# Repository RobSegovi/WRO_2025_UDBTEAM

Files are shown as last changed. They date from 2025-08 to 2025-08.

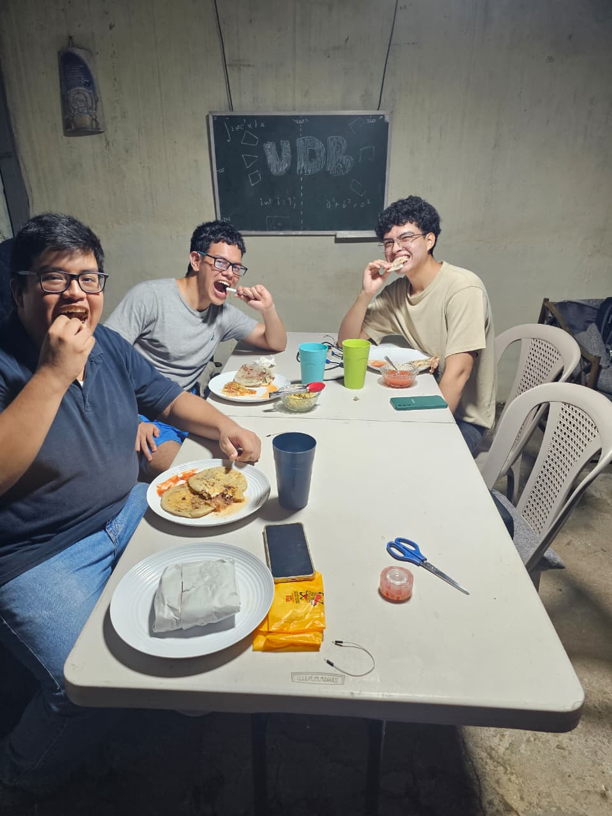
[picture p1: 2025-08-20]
T-photos/Funny Team.jpeg

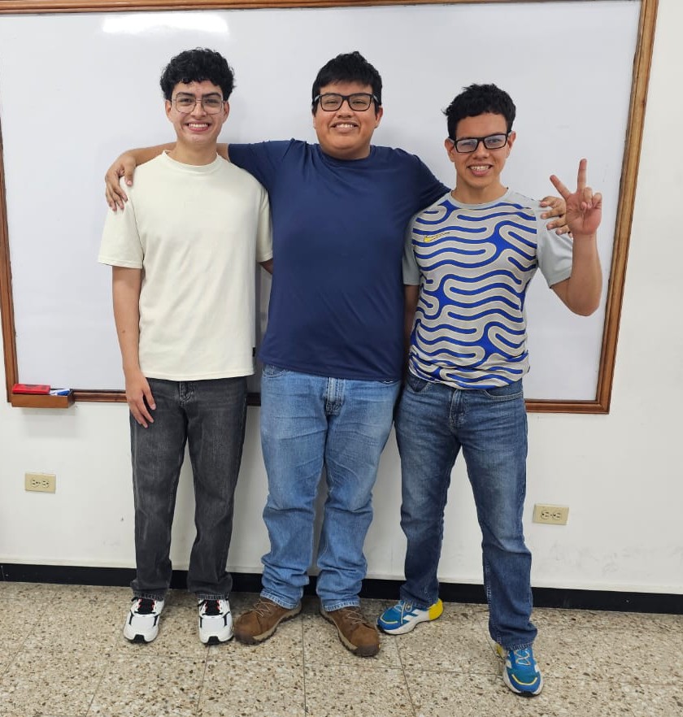
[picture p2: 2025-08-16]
T-photos/Team.jpeg

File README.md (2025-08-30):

# WRO_2025_UDBTEAM
Proyecto del vehículo autónomo para WRO 2025 - Futuros Ingenieros

<div align="center">

</div>

## Content

* `t-photos` contains 2 photos of the team 
* `video` contains the video.md file with the link to a video where driving demonstration exists
* `src` contains code of control software for all components which were programmed to participate in the competition
* `other` contains our training model for cubes based on yolo8

## Introduction
### Steering 
To control the vehicle direction, we adapted the tires form an RC car and implemented a steering mechanism that transforms the rotational motion of the servo motor (model G995) into rotational motion along a different axis as shown in image.  The servo motor provides enough torque to steer the vehicle while allowing precise control of the steering angle.



### Traction
The traction mechanism was disassembled from the RC car and integrated into the chassis of our vehicle.  The mechanism consists of three large gears that increase the torque of the DC motor, along with a smaller gear that connects the motor shaft to the three larger gears. The DC motor is controlled by an H bridge (L298 Module), which allows rotation in two directions to move the car forward and backward. The module can supply up to 35V and 2A, which is sufficient power for the motor. 



### Power sources 
A power bank  that supplies up to 5V at 3A powers the Raspberry Pi5, which requires a 5V at 5A but can also run on 5V at 3A.  The Raspberry Pi5 supplies power to the Arduino Mega via USB.
Two JYD 18650 batteries connected in series provide up to 8.2V, which is regulated to 6.5V by an LM2596 voltage regulator. This maintains a stable supply for the servo motor and H bridge, even as the batteries discharge.
Two separate power sources are used because a single power source capable of supplying both the Raspberry Pi5 and motors was not available.

<div align="center">

</div>

### Turning the car on and off
A switch connecting GND and the negative terminal of the battery is used to turn the motor and servo motor on and off. The power button on the Raspberry Pi5 is used to turn the Raspberry Pi5 and the Arduino Mega on and off.

### Articial vision
Our car can see its surroundings through a webcam connected via USB to a Raspberry Pi5, which processes the video input using python scripts with Open CV and a YOLO model trained on our dataset of images of red and green cubes.

### Information gathering Open challenge
Raspberry Pi 5 processes the information received from the webcam with three Python scripts. The main one is called xd.py and receives information from detectarcolor.py, which sends data to xd.py when it detects that enough pixels inside the area of interest fall within the blue or orange HSV threshold. xd.py also receives information from detectarpared.py when enough dark pixels are detected inside six different areas of interest: four detect the walls on the sides of the vehicle, one is positioned near the upper edge of the image to detect an incoming wall from the front, and another is located at the bottom center of the screen to detect when the vehicle is too close to a wall.

### Decision making Open challenge
The vehicle moves forward until it detects the blue or orange strips on the floor. A blue detection means the robot must steer to the right and ignore the orange strips. If an orange strip is detected, the robot does the opposite. After this, the vehicle will try to follow the inner walls, having three possible states: too close to the inner wall, close enough, or too far from the inner wall. The vehicle steers as needed to keep itself close enough to the inner wall until it detects a strip of the correct color and repeats the process.

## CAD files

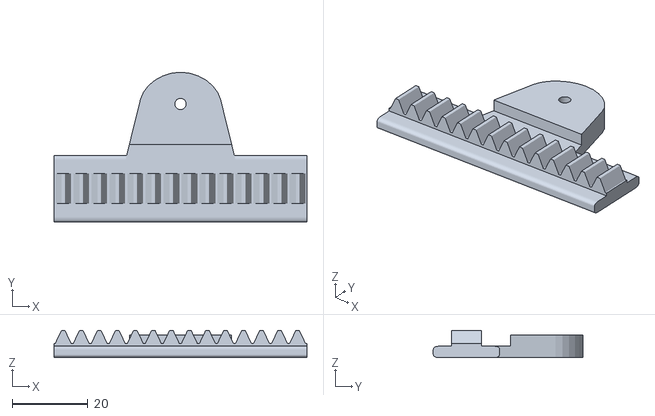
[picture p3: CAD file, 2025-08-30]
Models/Mecanismos UDB WRO/WRO-Cremallera.stl
67.0 x 39.6 x 7.18

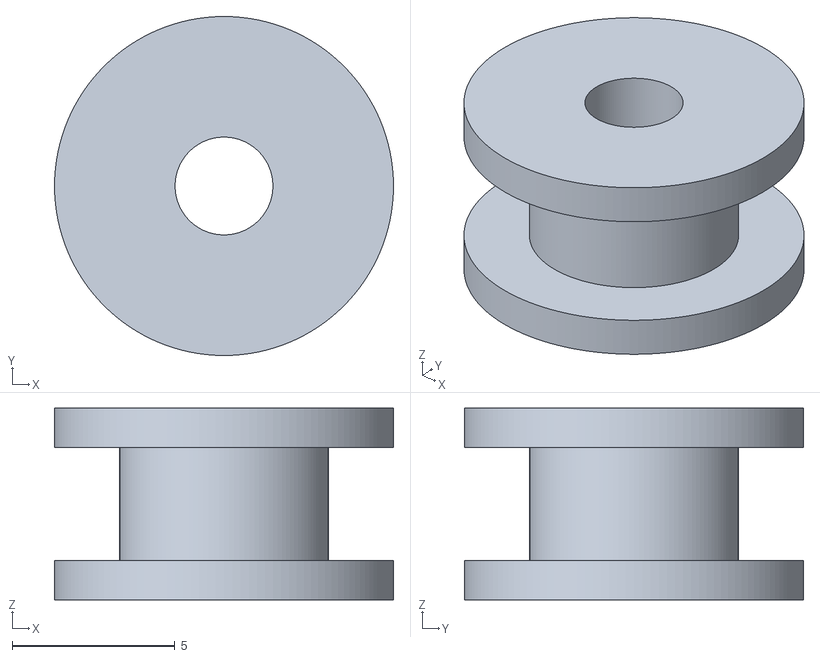
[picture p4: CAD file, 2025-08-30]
Models/Mecanismos UDB WRO/WRO-DeslizadorAcople.stl
10.4 x 10.4 x 5.88

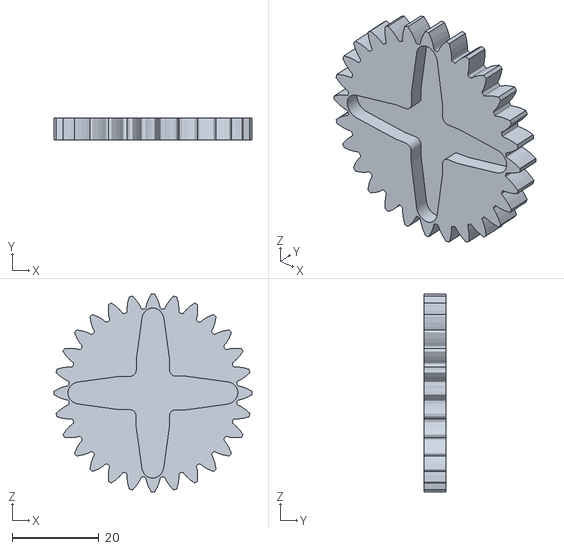
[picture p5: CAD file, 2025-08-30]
Models/Mecanismos UDB WRO/WRO-Engranaje.stl
45.6 x 5.00 x 45.6

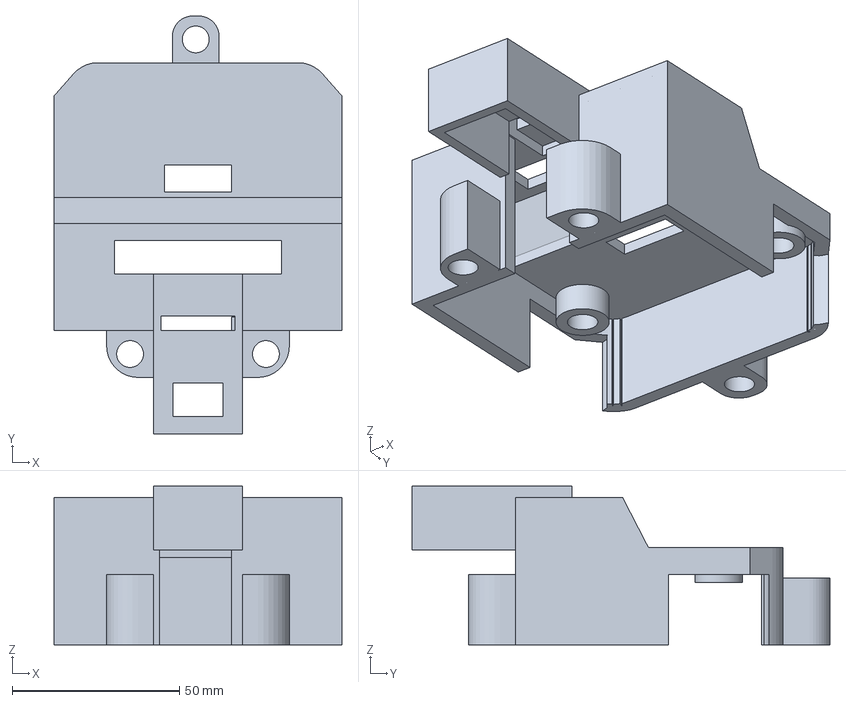
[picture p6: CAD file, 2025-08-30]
Models/Mecanismos UDB WRO/WRO-Tapa.3mf
86.0 x 124.9 x 47.4 mm

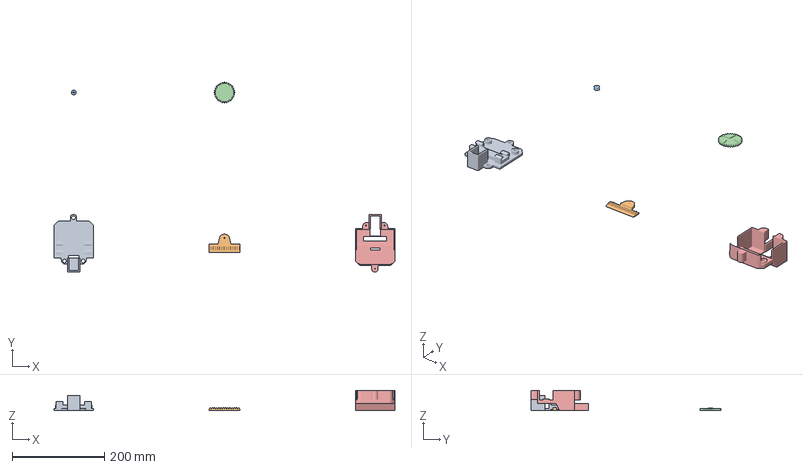
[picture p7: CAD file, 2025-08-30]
Models/Mecanismos UDB WRO/WRO-Base.3mf
741.2 x 412.8 x 44.1 mm
WRO-Base.stl
WRO-Cremallera.stl
WRO-DeslizadorAcople.stl
WRO-Engranaje.stl
WRO-Tapa.stl

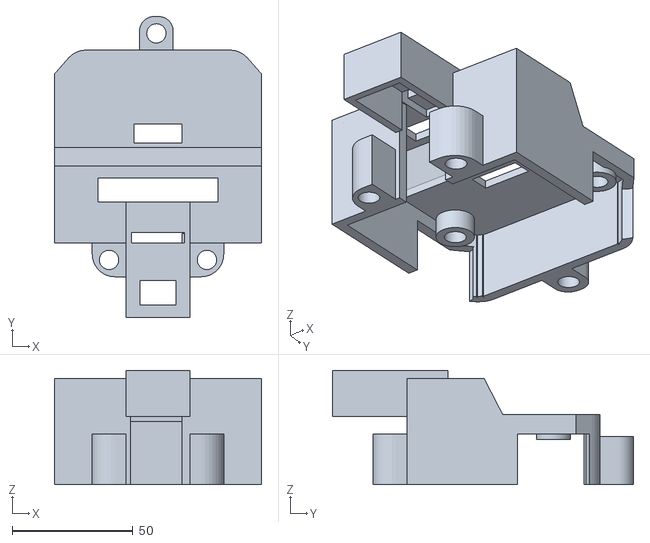
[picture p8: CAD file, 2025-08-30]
Models/Mecanismos UDB WRO/WRO-Cubo.006.stl
86.0 x 124.9 x 47.4

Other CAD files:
Models/Mecanismos UDB WRO/WRO-Base.stl
Models/Mecanismos UDB WRO/WRO.blend

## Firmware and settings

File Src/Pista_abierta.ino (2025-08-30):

#include <Wire.h> 
#include <LiquidCrystal_I2C.h>
//retroceso cuadno va a la izquierda es mucho y retroceso cuando va a derecha es muy poco 
//volataje og 6.70
//act 6.50
int pinServo = 10;
float y;
int theta = 0;
int imp=0;
LiquidCrystal_I2C lcd(0x27,16,2); 

// Definir un carácter personalizado (ejemplo: carita feliz)
byte up[8] = 
{
  B00100,
  B01110,
  B11111,
  B00100,
  B00100,
  B00100,
  B01110,
};
byte down[8] = 
{
  B01110,
  B00100,
  B00100,
  B00100,
  B11111,
  B01110,
  B00100,
};

// -- Motor --
int M1 = 4;
int M2 = 3;
int PWM = 2;

// --- tiempo ---  
long tiempo = 3000;
long tiempoactual = 0;
int numdelay = 72;
int numdelayexiz = 30;
int numdelayexde = 40 ;
int retrodelay = 800;
int delaygiz = 2200;
int delaygde = 2200;
// ---Varaibles de velocidad 
int vcorriz = 225;
int vcorrde =225;
int vgiriz = 245;
int vgirde = 245;
int vretro = 255;
int vavan =  200;
// --- Variables de comunicación ---
String inputString = "";
bool stringComplete = false;

// --- Variables Py ---
int indicador =0 ;   // 0 = nada, 1 = verde, 2 = rojo, 3 = naranjaDer, 4 = azulIzq, 5 = pared, 6 = correcion derecha, 7 = correcion izquierda.
long posX = 0;        // coordenada eje X
long area = 0;        // área del objeto
int guardar = 0;      //guardar indicador
int color = 0;
// --- milis const ---
unsigned long  tanterior = 0;
unsigned long esperadecor = 500;
unsigned long esperadecorder = 620;
unsigned long tinicio = 0;
bool prim = true;
bool corregir = false;
void setup() 
{
  origen(0);
  pinMode(pinServo, OUTPUT);
  lcd.init();
  lcd.backlight();
  lcd.createChar(0, up);
  lcd.createChar(1, down);
  delay(10);
  lcd.print("c:");
  for(int i = 2; i < 5; i++)
  {
    pinMode(i, OUTPUT);
  }

  Serial.begin(9600);
  digitalWrite(M1, LOW);
  digitalWrite(M2, LOW);

}
void loop()
{

  lectura();
  //avanzar 
  
  inicio: 
  if(posX==1) {
    color=1;
    lcd.setCursor(10,1);
    lcd.print("     ");
    lcd.setCursor(10,1);
    lcd.print("c:azul");
  }
  else if (posX==2){
    color=2;
        lcd.setCursor(10,1);
    lcd.print("     ");
    lcd.setCursor(10,1);
    lcd.print("c:naran");
  }

  if(indicador == 1)
  {
    pantalla(1);
    if (guardar == 2) // anterioriormente corriegio a la derecha
    {
      /*/izquierda(75, vcorriz, 10);//(angulo,velocidad,delay)
      for (int i=0 ; i<=numdelay; i++)
      {
       lectura();
       if(indicador== 4 || indicador == 5) goto inicio;
       delay(10);
      }/*/
    }
    else if (guardar == 3)//anteriormente corrigio a la izquierda
    {
     /*/ derecha(50, vcorrde, 10);//(angulo,velocidad,delay)
      for (int i=0 ; i<=numdelay; i++)
      {
       lectura();
       if(indicador== 4 || indicador == 5) goto inicio;
       delay(10);
      }/*/
    }
    else if(guardar == 5 )//girar a la derecha
    {
      origen(2);
    }
    else if( guardar == 4 )//girar a la izquierda
    {
      origen(1);
    }
    else origen(0);
    if(imp==0)
    {
      avanzar(245);
      delay(100);
      imp =1;
    }else
    {
    avanzar(vavan);
    guardar = indicador;
    }
    
    
  }
  else if(indicador == 2)//corregir a la derecha
  {
    unsigned long tactual = millis();  
    if(prim == true)
    {
      tinicio =  millis();
      prim = false;
    }
    if((tactual - tinicio) >= esperadecorder)
    {
      izquierda(75, vcorriz, 10);//(angulo,velocidad,delay)
      for (int i=0 ; i<=numdelayexde; i++)
      {
       lectura();
       if(indicador !=2)
        {
         prim =true;
         goto inicio;
        }
       delay(10);
      }


      prim =true;
      
      
    }
    pantalla(5);
    derecha(40, vcorrde, 0);//(angulo,velocidad,delay)
    guardar = indicador;
  }
  else if(indicador == 3)//correcion izquierda
  {
   
    unsigned long tactual = millis();  
    if(prim == true)
    {
      tinicio =  millis();
      prim = false;
    }
    if(tactual-tinicio >= esperadecor)
    {
      derecha(50, vcorriz, 300);//(angulo,velocidad,delay)
      for (int i=0 ; i<=numdelayexiz; i++)
      {
       lectura();
       if(indicador !=3)
        {
         prim =true;
         goto inicio;
        }
       delay(10);
      }

      prim =true;
      
      
    }
    pantalla(6);
    izquierda(71, vcorriz, 0);//(angulo,velocidad,delay)
    guardar = indicador;

  }
  //girar  a la izquierda
  else if(indicador == 4)//color azul
  {
    pantalla(4);
    izquierda(90, vgiriz, delaygiz);//(angulo,velocidad,delay)
    guardar = indicador;
    color = 1;
    lcd.setCursor(10,1);
    lcd.print("     ");
    lcd.setCursor(10,1);
    lcd.print("c:azul");
    
  }
  //girar a la derecha derecha
  else if(indicador == 5)//color naranja
  {
    pantalla(3);
    derecha(40, vgirde, delaygde);//(angulo,velocidad,delay)
    guardar = indicador;
    color = 2;
    lcd.setCursor(10,1);
    lcd.print("     ");
    lcd.setCursor(10,1);
    lcd.print("c:naran");
  }
   else if(indicador == 6)//pared, entonces retroceder y girar
  {
    pantalla(2); 
    if(guardar == 5 || color == 2)//girar a la derecha
    {
      Servo(90);// girar a la izquierda para movernos a la derecha
      retroceder(vretro);
      delay(retrodelay);
      //derecha(40, 225, 1500);//(angulo,velocidad,delay)
    }
    else if(guardar == 4 || color == 1)//girar a la izquierda
    {
      Servo(40);
      retroceder(vretro);
      delay(retrodelay);
      //izquierda(90, 225, 1500);//(angulo,velocidad,delay)
      
    }
    guardar = indicador;
  }
  

}

// --- Funciones de movimiento ---
void avanzar(int fast) 
{
  analogWrite(PWM, fast);
  digitalWrite(M1, HIGH);
  digitalWrite(M2, LOW);

}

void retroceder(int fast) 
{
  analogWrite(PWM, fast);
  digitalWrite(M1, LOW);
  digitalWrite(M2, HIGH);

}

void detener() 
{
  digitalWrite(M1, LOW);
  digitalWrite(M2, LOW);

}

void izquierda(int ang, int vel, int re)
{
  Servo(ang); //centro 
  avanzar(vel);
  delay(re);
}

void derecha(int ang, int vel, int re)
{
  Servo(ang); //centro 
  avanzar(vel);
  delay(re);

}

void origen(int k)
{
  if(k == 0) theta=66; //origen real.
  else if(k == 1) theta=68; //origen izquierda. viene de la izquierda
  else if(k == 2) theta=70; //origen derecha. viende de la izquierda
  Servo(theta);

}

// --- Servo sin libreria---
void Servo(float theta)
{
  for(int hz = 0; hz <= 50; hz++)
  {
    y = ((theta*2000.0)/180.0) + 500.0;
    digitalWrite(pinServo, HIGH);
    delayMicroseconds(y);
    digitalWrite(pinServo, LOW);
    delayMicroseconds(2000.0 - y);
    
  }
}

// --- LCD ---
void pantalla(int tv)
{
  if(tv == 1)
  {
    lcd.setCursor(0,0);
    lcd.write((byte)0);
    lcd.write((byte)0);
    lcd.write((byte)0);
    lcd.write((byte)0); 
    lcd.setCursor(0,1);
    lcd.write((byte)0);
    lcd.write((byte)0);
    lcd.write((byte)0);
    lcd.write((byte)0); 
  }
  else if(tv == 2)
  {
    lcd.setCursor(0,0);
    lcd.write((byte)1);
    lcd.write((byte)1);
    lcd.write((byte)1);
    lcd.write((byte)1); 
    lcd.setCursor(0,1);
    lcd.write((byte)1);
    lcd.write((byte)1);
    lcd.write((byte)1);
    lcd.write((byte)1);
  }
  else if(tv == 3)
  {
    lcd.setCursor(0,0);
    lcd.print(">>>>");
    lcd.setCursor(0,1);
    lcd.print(">>>>");
  }
  else if(tv == 4)
  {
    lcd.setCursor(0,0);
    lcd.print("<<<<");
    lcd.setCursor(0,1);
    lcd.print("<<<<");
  }
   else if(tv == 5)
  {
    lcd.setCursor(0,0);
    lcd.print("-->>");
    lcd.setCursor(0,1);
    lcd.print("-->>");
  }
    else if(tv == 6)
  {
    lcd.setCursor(0,0);
    lcd.print("<<--");
    lcd.setCursor(0,1);
    lcd.print("<<--");
  }

}

// --- Lectura de datos desde la Raspberry ---
void lectura()
{
  if (stringComplete) 
  {
    stringComplete = false;

    // Separar por comas
    int firstComma = inputString.indexOf(',');
    int secondComma = inputString.indexOf(',', firstComma + 1);

    if (firstComma > 0 && secondComma > 0) 
    {
      // Extraer las 3 partes
      String indicadorStr = inputString.substring(0, firstComma);
      String xStr = inputString.substring(firstComma + 1, secondComma);
      String areaStr = inputString.substring(secondComma + 1);

      // Convertir a enteros
      indicador = indicadorStr.toInt();
      posX = xStr.toInt();
      area = areaStr.toInt();
      //delay(20);
      String LCDP0 = "i:" + String(indicador);

      

      lcd.setCursor(10,0);
      lcd.print(LCDP0);
      
     
    }
    inputString = ""; // limpiar para el siguiente mensaje
  }
}

// --- Captura de datos entrantes por Serial ---
void serialEvent() 
{
  while (Serial.available()) 
  {
    char inChar = (char)Serial.read();
    if (inChar == '\n') // fin del mensaje
    {       
      stringComplete = true;
    } 
    else 
    {
      inputString += inChar;
    }
  }
}

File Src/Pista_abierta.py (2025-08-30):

# Detectar y clasificar objetos en tiempo real
# pylint: disable=no-member
import time
from ultralytics import YOLO
import cv2
import serial
import numpy as np
from color import lineas
from pared import pared
from roi import interior

# Configurar Arduino y el puerto

def abrir_puerto():
    while True:
        try:
            s = serial.Serial(
                port='/dev/ttyACM0',
                baudrate=9600,
                timeout=1,
                rtscts=False,
                dsrdtr=False
            )
            # evitar reset
            s.dtr = False
            s.rts = False
            time.sleep(2)  # darle tiempo al arduino
            s.reset_input_buffer()
            s.reset_output_buffer()
            print("? Puerto serie abierto correctamente")
            return s
        except serial.SerialException as e:
            print("No pude abrir el puerto, reintentando:", e)
            time.sleep(1)
            
# abrir puerto
arduino = abrir_puerto()
 
# Cargar modelo YOLO
model = YOLO("cubos1.pt")

# Abrir la camara
cap = cv2.VideoCapture(0)
cap.set(3, 320)  # ancho
cap.set(4, 240)  # alto

n = 0
results = []
conteo=0
giro = 0
lado = 0
time.sleep(3)
prim = 0
x = 0

while True:
    ret, frame = cap.read()
    if not ret:
        print("No se pudo leer la camara")
        break
    conteo += 1
    # Solo analizar cada 2 frames
    if conteo % 2 == 0:
        results = model(frame)

    h, b, _ = frame.shape
    maxArea = 0
    objCercano = ""
    #x = 0
    y = 0
    contador = 0
    linea = 0
    p = 0
    
    indicador = 0
    

    # Color de la linea
    linea, pixnaranja, pixazul = lineas(frame,  n)

    # Detectar pared
    p = pared(frame,lado)
    
    a = interior(frame,linea,giro,lado)
    if a == 4:
        giro = 1
    elif a == 6 or a == 7:
        giro = 0
    elif a == 13:
        lado = 1 # Lado derecho
        x=2
    elif a == 14:
        lado = 2 # Lado izquierdo
        x=1

                                              #h-75
    cv2.rectangle(frame, (b//3, h-90), (2*b//3, h), (0, 255, 0), 2) #rectangulo detecta pared
    cv2.rectangle(frame, (126, h-75), (193, h-45), (0, 255, 0), 2) #rectangulo detecta lineas 

    # Preparar mensaje para Arduino
 
    if lado == 0:
        indicador = "1" #AVANZAR
    elif a == 1:
        indicador = "1" #AVANZAR
    elif a == 2:
        indicador = "2" #CORREGIR A LA DERECHA
    elif a == 3:
        indicador = "3" #CORREGIR A LA IZQUIERDA
    elif a == 4:
        indicador = "1" #AVANZAR
        if lado == 2:
            x = 1
        if lado == 1:
            x = 2
    elif a == 5:
        indicador = "1" #AVANZAR
    elif a == 6:
        indicador = "4" #GIRO A LA IZQUIERDA CON DELAY
        mensaje = f"{indicador},{x},{maxArea}\n"
        for _ in range(10):
                arduino.write(mensaje.encode())
                print("4444")
                time.sleep(0.1)
        
    elif a == 7:  
        indicador = "5" #GIRO A LA DERECHA CON DELAY
        mensaje = f"{indicador},{x},{maxArea}\n"
        for _ in range(10):
                arduino.write(mensaje.encode())
                print("5555")
                time.sleep(0.1)
 
    if p == 5:
        indicador = "6" #DETENER Y RETROCEDER
    
    mensaje = f"{indicador},{x},{maxArea}\n"

    #impresion de valores en cmdp
    print(f"{mensaje} n:{n} linea:{linea} pN:{pixnaranja} pB:{pixazul} a:{a}")
    
    
    # enviar mensaje al arduino
    try:
        arduino.write(mensaje.encode())
    except serial.SerialException as e:
        print("?? Error de escritura, reabriendo puerto:", e)
        try:
            arduino.close()
        except:
            pass
        time.sleep(0.5)
        arduino = abrir_puerto()
        
        
    # Mostrar video en ventana
    cv2.imshow("Resultado", frame)
    if cv2.waitKey(1) & 0xFF == ord('q'):
        break

cap.release()
cv2.destroyAllWindows()


if arduino.is_open:
    arduino.close()
    print("? se cerro el puerto")

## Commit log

2025-07-30 Prueba de imagenes con coordenadas
2025-07-30 Cambio de la posición de la etiqueta
2025-07-30 Cambios para prueba
2025-08-02 cambio de tamaño de circulo
2025-08-11 Imprimir mensaje para mandar al arduino
2025-08-11 Mandar mensaje a arduino
2025-08-14 Video en tiempo real con raspberry con detección
2025-08-16 Creación de carpetas
2025-08-18 Detección de pared (17/09/25)
2025-08-20 Detectar colores en el piso y tomar decisiones
2025-08-21 pequeños cambios para la detección de color
2025-08-21 Cambios de detección de color
2025-08-22 Detecta colores y la pared
2025-08-23 Codigo para la raspberry
2025-08-25 Codigo para pista abierta
2025-08-25 Codigo para pista abierta (1er intento)
2025-08-25 pequeños cambios de color azul
2025-08-29 Cambios para pista abierta
2025-08-30 Impresiones en 3D
    [WRO-Base.3mf, WRO-Base.stl, WRO-Cremallera.stl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]
